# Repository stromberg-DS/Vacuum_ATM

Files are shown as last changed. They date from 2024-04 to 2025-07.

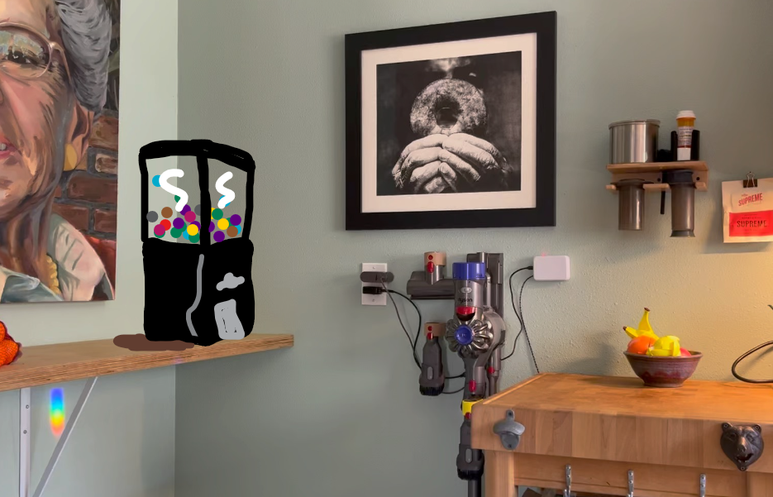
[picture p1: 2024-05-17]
Images/OriginalLocation.png

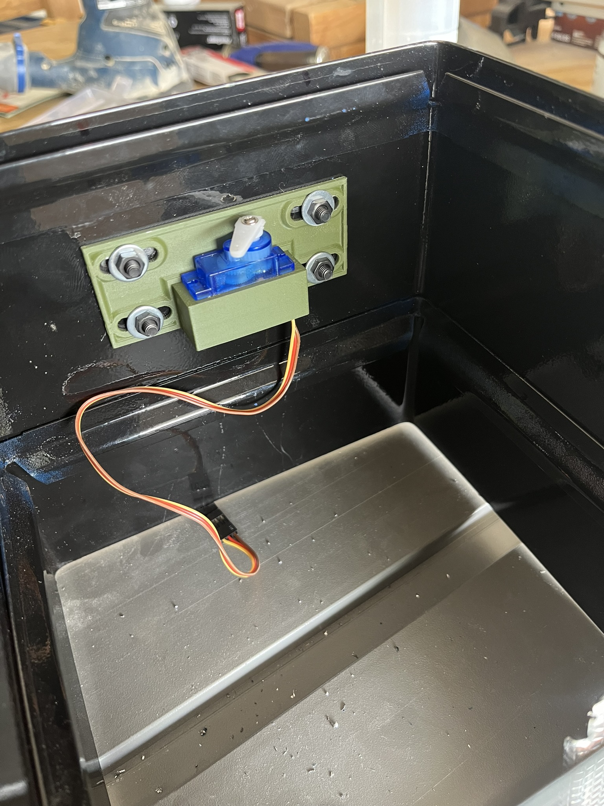
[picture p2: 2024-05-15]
Images/ServoMount.JPEG

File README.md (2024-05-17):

# Vacuum_ATM
Automatically reward the first person who vacuums the floor.

This is a project that tracks the dust levels in your house and tells you when to vacuum. A Photon 2 microcontroller detects when the vacuum is removed/replaced. Meanwhile a separate Photon 2 mounted inside a toy vending machine tracks if you have vacuumed for long enough to get a reward. If you have vacuumed long enough, you can turn the crank and get a plastic capsule filled with whatever (money, candy, etc).

## Directory

**Vacuum_ATM** - This folder contains the code for the dispensing side of the system.

**Vacuum_Status** - This folder contains the code for the photon that senses the presence of the vacuum.

**3D_Models** - Models to print out to get everything to work.

**Cut_Files** - Files to cut on a CNC router or laser cutter.

**Wiring Diagram** - Images of the wiring of both the Vacuum ATM and the Vacuum Status Photons.

**Testing** - Where I did all of my initial R&D. Actually I'm kind of embarassed that you would even want to look in here. Go back up to 3D_models. This is not a good look for you.

More information can be found at [my Hackster.io writeup](https://www.hackster.io/blotlat/vacuum-atm-a74ef9)

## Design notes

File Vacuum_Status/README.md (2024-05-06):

# Vacuum_Status

This firmware project was created using [Particle Developer Tools](https://www.particle.io/developer-tools/) and is compatible with all [Particle Devices](https://www.particle.io/devices/).

Feel free to replace this README.md file with your own content, or keep it for reference.

## Table of Contents
- [Introduction](#introduction)
- [Prerequisites To Use This Template](#prerequisites-to-use-this-repository)
- [Getting Started](#getting-started)
- [Particle Firmware At A Glance](#particle-firmware-at-a-glance)
  - [Logging](#logging)
  - [Setup and Loop](#setup-and-loop)
  - [Delays and Timing](#delays-and-timing)
  - [Testing and Debugging](#testing-and-debugging)
  - [GitHub Actions (CI/CD)](#github-actions-cicd)
  - [OTA](#ota)
- [Support and Feedback](#support-and-feedback)
- [Version](#version)

## Introduction

For an in-depth understanding of this project template, please refer to our [documentation](https://docs.particle.io/firmware/best-practices/firmware-template/).

## Prerequisites To Use This Repository

To use this software/firmware on a device, you'll need:

- A [Particle Device](https://www.particle.io/devices/).
- Windows/Mac/Linux for building the software and flashing it to a device.
- [Particle Development Tools](https://docs.particle.io/getting-started/developer-tools/developer-tools/) installed and set up on your computer.
- Optionally, a nice cup of tea (and perhaps a biscuit).

## Getting Started

1. While not essential, we recommend running the [device setup process](https://setup.particle.io/) on your Particle device first. This ensures your device's firmware is up-to-date and you have a solid baseline to start from.

2. If you haven't already, open this project in Visual Studio Code (File -> Open Folder). Then [compile and flash](https://docs.particle.io/getting-started/developer-tools/workbench/#cloud-build-and-flash) your device. Ensure your device's USB port is connected to your computer.

3. Verify the device's operation by monitoring its logging output:
    - In Visual Studio Code with the Particle Plugin, open the [command palette](https://docs.particle.io/getting-started/developer-tools/workbench/#particle-commands) and choose "Particle: Serial Monitor".
    - Or, using the Particle CLI, execute:
    ```
    particle serial monitor --follow
    ```

4. Uncomment the code at the bottom of the cpp file in your src directory to publish to the Particle Cloud! Login to console.particle.io to view your devices events in real time.

5. Customize this project! For firmware details, see [Particle firmware](https://docs.particle.io/reference/device-os/api/introduction/getting-started/). For information on the project's directory structure, visit [this link](https://docs.particle.io/firmware/best-practices/firmware-template/#project-overview).

## Particle Firmware At A Glance

### Logging

The firmware includes a [logging library](https://docs.particle.io/reference/device-os/api/logging/logger-class/). You can display messages at different levels and filter them:

```
Log.trace("This is trace message");
Log.info("This is info message");
Log.warn("This is warn message");
Log.error("This is error message");
```

### Setup and Loop

Particle projects originate from the Wiring/Processing framework, which is based on C++. Typically, one-time setup functions are placed in `setup()`, and the main application runs from the `loop()` function.

For advanced scenarios, explore our [threading support](https://docs.particle.io/firmware/software-design/threading-explainer/).

### Delays and Timing

By default, the setup() and loop() functions are blocking whilst they run, meaning that if you put in a delay, your entire application will wait for that delay to finish before anything else can run. 

For techniques that allow you to run multiple tasks in parallel without creating threads, checkout the code example [here](https://docs.particle.io/firmware/best-practices/firmware-template/).

(Note: Although using `delay()` isn't recommended for best practices, it's acceptable for testing.)

### Testing and Debugging

For firmware testing and debugging guidance, check [this documentation](https://docs.particle.io/troubleshooting/guides/build-tools-troubleshooting/debugging-firmware-builds/).

### GitHub Actions (CI/CD)

This project provides a YAML file for GitHub, automating firmware compilation whenever changes are pushed. More details on [Particle GitHub Actions](https://docs.particle.io/firmware/best-practices/github-actions/) are available.

### OTA

To learn how to utilize Particle's OTA service for device updates, consult [this documentation](https://docs.particle.io/getting-started/cloud/ota-updates/).

Test OTA with the 'Particle: Cloud Flash' command in Visual Studio Code or the CLI command 'particle flash'!

This firmware supports binary assets in OTA packages, allowing the inclusion of audio, images, configurations, and external microcontroller firmware. More details are [here](https://docs.particle.io/reference/device-os/api/asset-ota/asset-ota/).

## Support and Feedback

For support or feedback on this template or any Particle products, please join our [community](https://community.particle.io)!

## Version

Template version 1.0.2

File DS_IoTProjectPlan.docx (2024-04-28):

Project Name: Vacuum ATM
Student Name: Daniel Stromberg | Capstone Date:5/17/24

Project Motivation and Overview:

With 2 dogs and a cat, my house needs frequent vacuuming. Vacuuming always falls off the radar. The Vacuum ATM will incentivize anyone in the house to vacuum by dispensing a reward (cash or otherwise) after they vacuum. The Vacuum ATM will lock out any more rewards for several days, showing an alert when it is ready to give out another reward.

Cash will be dispensed either with rollers and a stepper motor, or through a modified capsule toy vending machine.

Minimum Features:

- Track the accumulation of dust over time.
- Track the amount of time that has passed since the last time the vacuum was used.
- Track whether the vacuum is charging or in use.
- Alert the household when the vacuum is ready to be used (when a reward will be dispensed for vacuuming). A simple LED would be a basic option.
- Reward the person who vacuumed (Basic option would be credits or leaderboard shown on a dashboard)

Desired Features:

- Show vacuum use on a dashboard (dust levels, how long until vacuum is ready, etc.).
- Dispense dollar bills (or other incentive) when user has vacuumed long enough.
- Send a text/email to let house members know the vacuum is ready to reward someone for vacuuming.

Stretch Goal Features:

- Get weather data and increase vacuuming frequency if wind is high.
- Detect who vacuumed (separate buttons).
- Use fingerprint sensor to ID who has vacuumed.

Anticipated Components:

- Reed Switch or Hall effect sensor
- ~~Stepper Motor & controller board (large motor if using toy dispenser)~~ – updated 4/28, opting for other option.
- Neopixels
- Fingerprint sensor

Concerns and Considerations (Project Risks and Potential Mitigations)

- How to detect if someone actually vacuums vs taking it off the wall, doing nothing, and replacing it?
- How to dispense rewards?

Other Information:

Project Implementation Timeline:
Tasks | 12-APR | 19-APR | 26-APR | 3-May | 10-May | 17-May
Project Plan | X
Plan Dispenser, order parts | | X
Make overall design | | | X
Test Vacuum logic w/basic parts | | | X
Design display | | | X
Build/assemble dispenser | | | | X
Final Assembly | | | | | X
Finish Hackster.io | | | | | X
Edit Video | | | | | | X
Finish Presentation & Video | | | | | | X
Capstone Presentation | | | | | | X

Internet of Things and Rapid Prototyping Bootcamp – Capstone Project Proposal

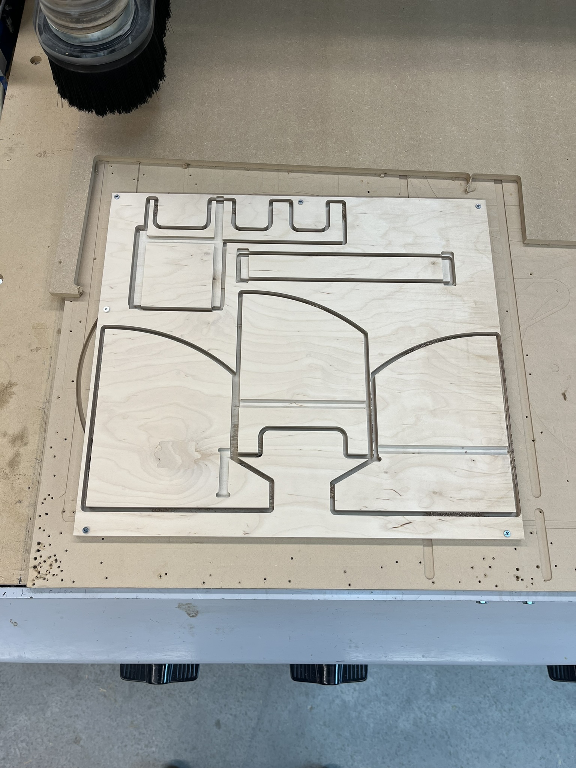
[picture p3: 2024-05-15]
Images/Panels.JPEG

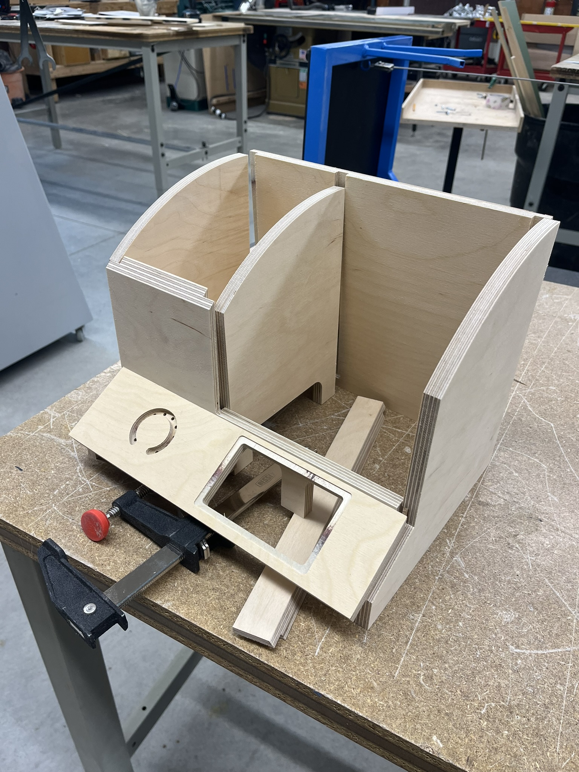
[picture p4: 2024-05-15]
Images/DryFit.JPEG

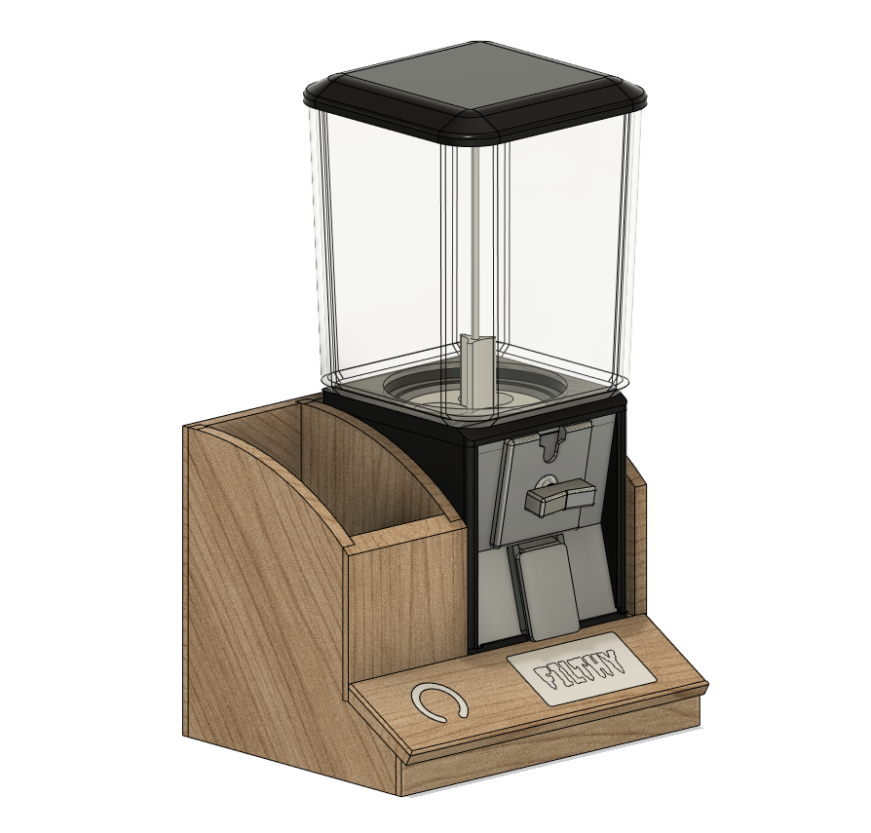
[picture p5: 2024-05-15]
Images/VacATM.png

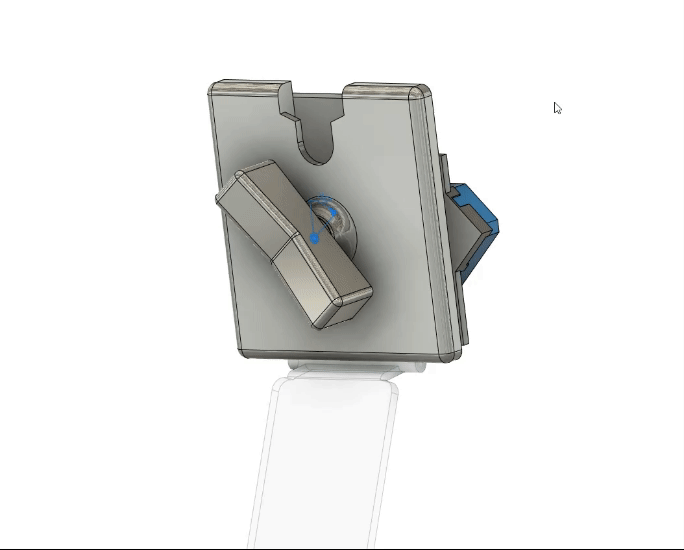
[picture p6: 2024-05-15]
Images/KnobTurning.gif

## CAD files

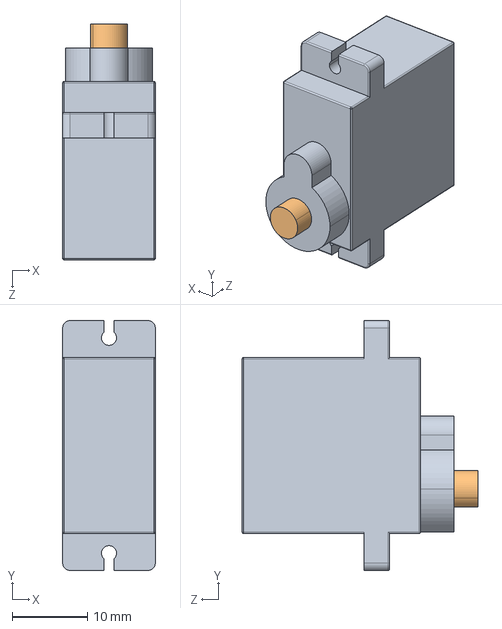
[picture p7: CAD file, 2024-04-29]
3D_Models/serwo 9g.STEP
12.3 x 33.2 x 31.3 mm
korpus
wał

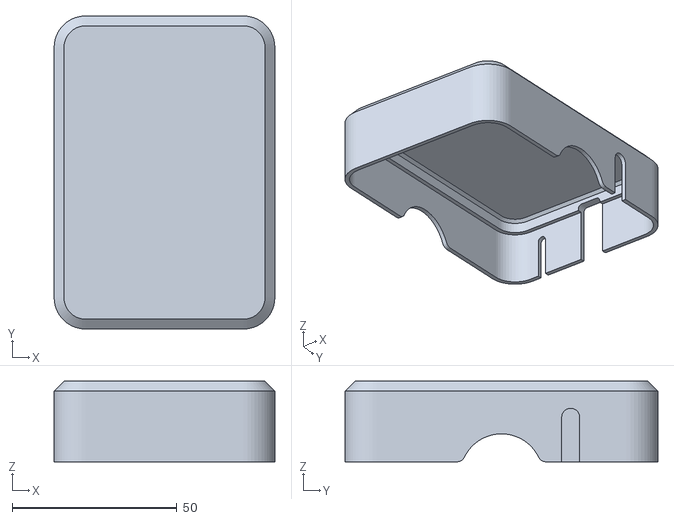
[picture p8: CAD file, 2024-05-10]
3D_Models/VacStatus_Case/CaseTop.stl
67.0 x 95.0 x 24.5

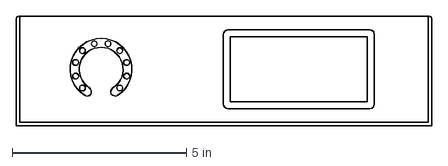
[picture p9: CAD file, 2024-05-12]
Cut_Files/Faceplate.dxf
11.9 x 3.15 in

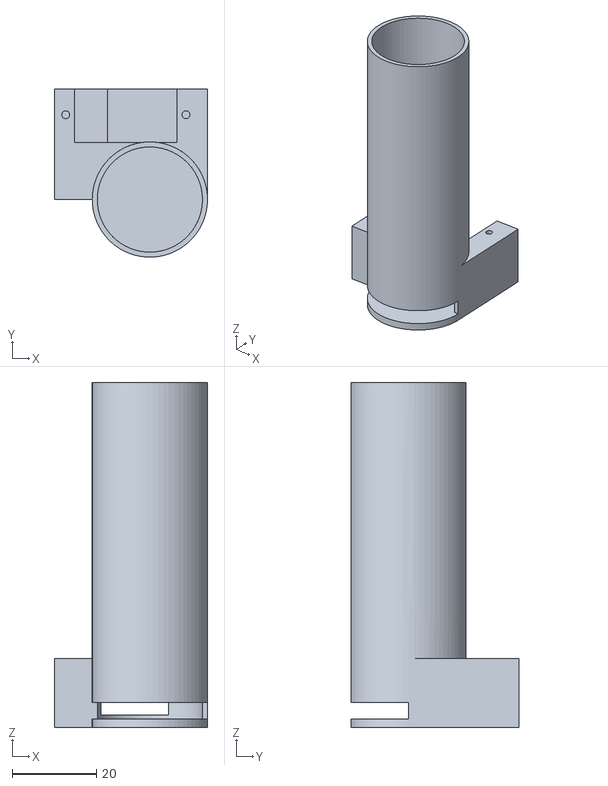
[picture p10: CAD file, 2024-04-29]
DispenseTube.stl
36.4 x 40.0 x 82.0

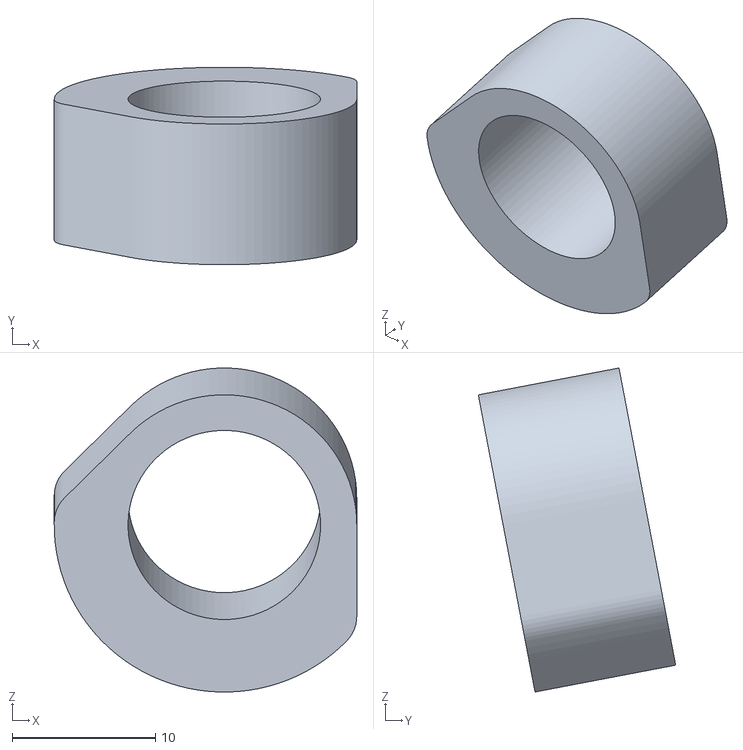
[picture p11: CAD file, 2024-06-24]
3D_Models/ATM_models/SwitchCam.stl
21.1 x 13.8 x 22.6

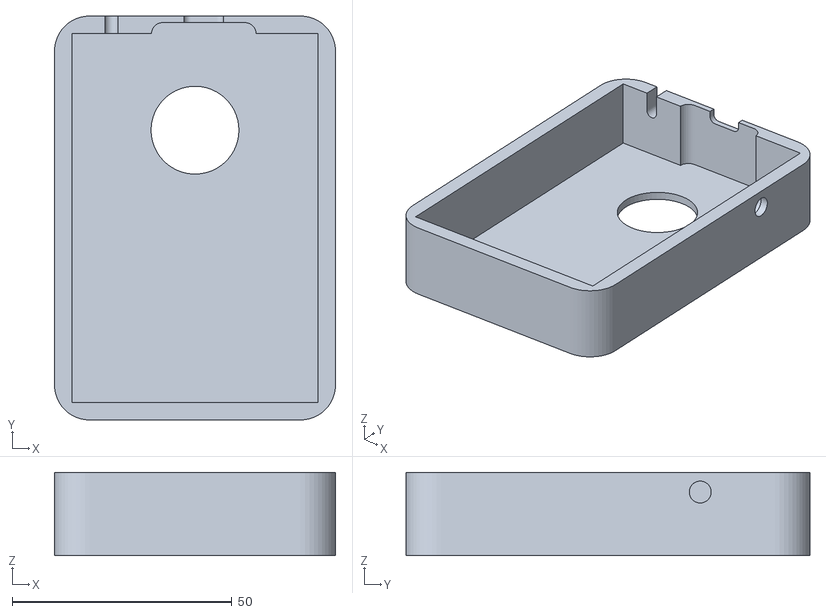
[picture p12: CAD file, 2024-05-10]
3D_Models/VacStatus_Case/CaseBottom.stl
64.0 x 92.0 x 19.0

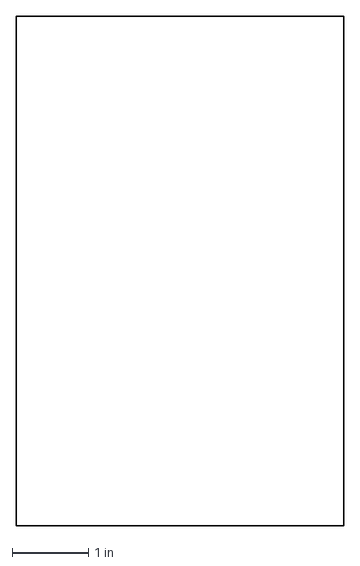
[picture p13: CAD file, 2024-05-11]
Cut_Files/Shelf.dxf
4.29 x 6.68 in

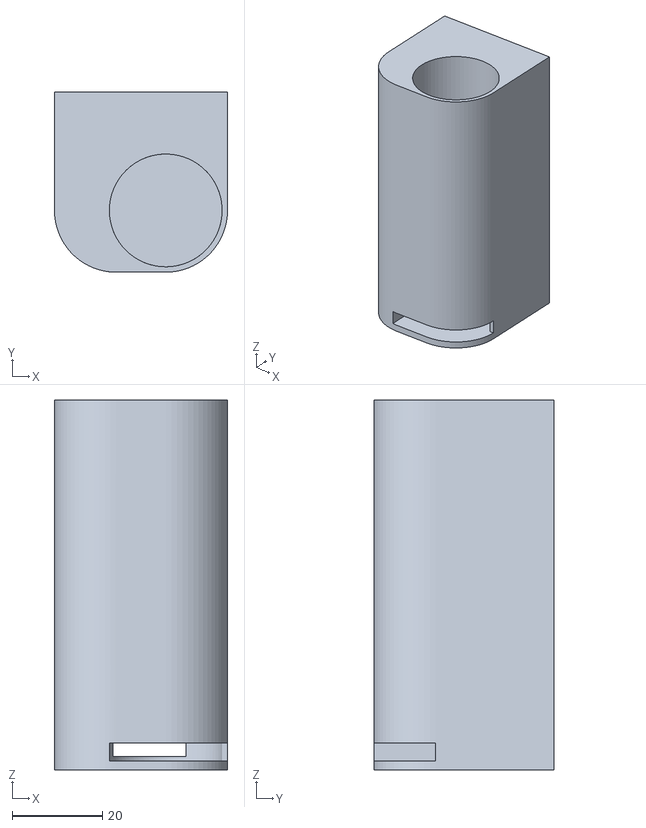
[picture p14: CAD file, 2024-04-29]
DispenseTubeV3.stl
38.4 x 40.0 x 82.0

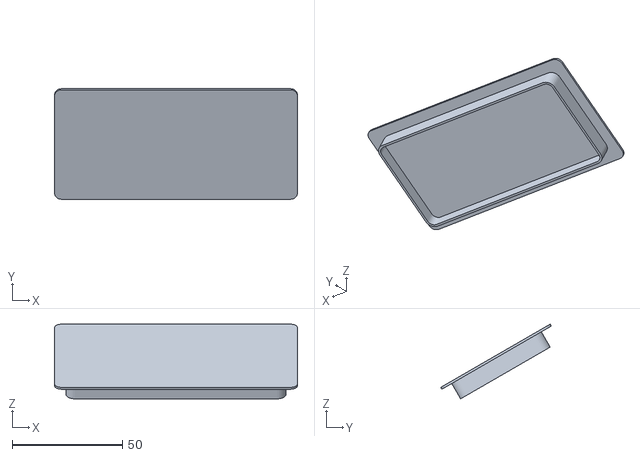
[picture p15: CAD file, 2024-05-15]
3D_Models/ATM_models/Display.stl
110.0 x 50.1 x 33.8

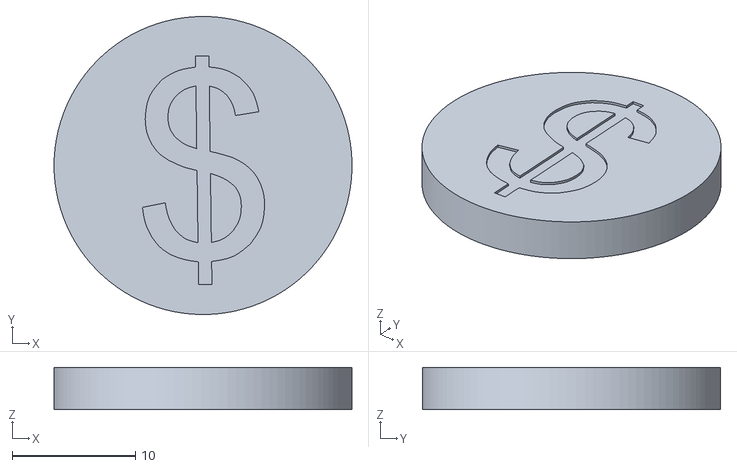
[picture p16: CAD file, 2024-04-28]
Coin.stl
24.2 x 24.2 x 3.43

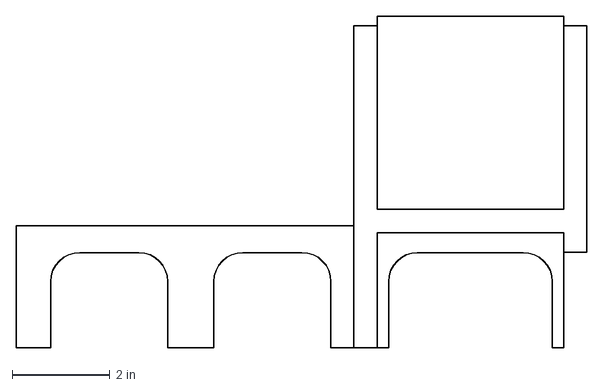
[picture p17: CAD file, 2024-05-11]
Cut_Files/Front.dxf
11.7 x 6.79 in

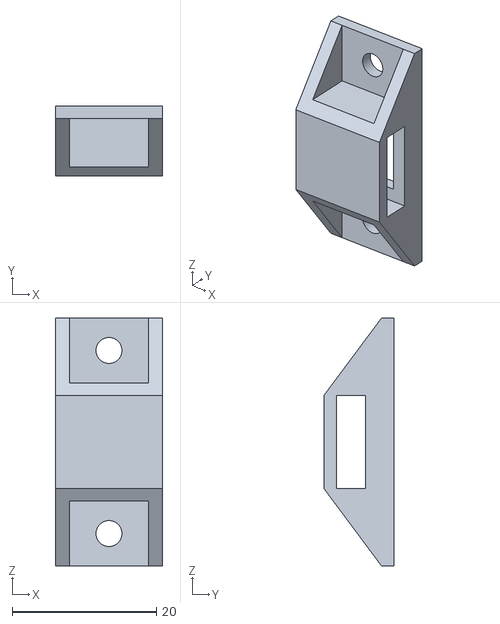
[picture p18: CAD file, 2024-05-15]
3D_Models/ATM_models/ButtonMount.stl
14.9 x 9.75 x 34.4

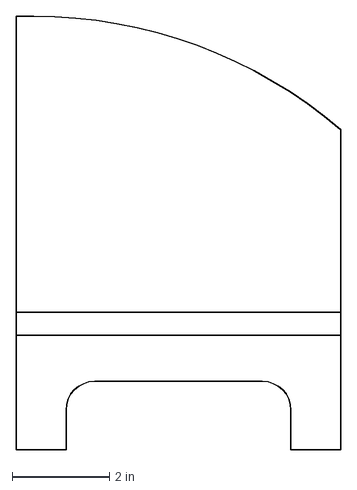
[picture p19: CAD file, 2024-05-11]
Cut_Files/Middle.dxf
6.68 x 8.93 in

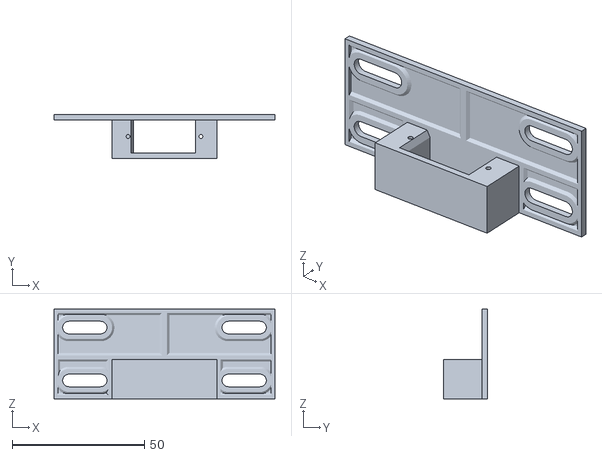
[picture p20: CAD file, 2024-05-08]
3D_Models/ATM_models/Servomount.stl
83.5 x 16.5 x 34.0

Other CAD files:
Cut_Files/Right.dxf
3D_Models/ATM_models/smSwitchMount.stl
Cut_Files/Back.dxf
3D_Models/ATM_models/HoleCover.stl
3D_Models/ATM_models/ShaftCollar.stl
3D_Models/ATM_models/SwitchCam_wSetScrew.stl
Cut_Files/FaceSupport.dxf
Cut_Files/Left.dxf

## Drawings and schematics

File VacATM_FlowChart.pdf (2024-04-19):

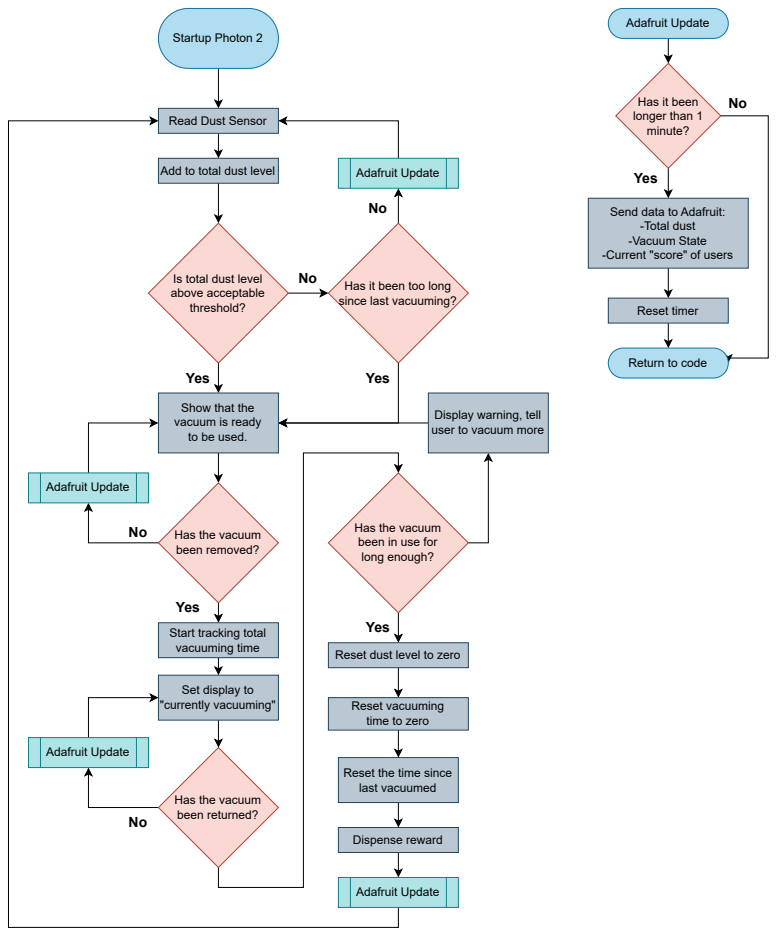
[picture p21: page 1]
Yes; Dispense reward; Startup Photon 2; Adafruit Update; Reset timer

Has it been
longer than 1
minute?

Read Dust Sensor

Add to total dust level

Send data to Adafruit:
-Total dust
-Vacuum State
-Current "score" of users

Is total dust level
above acceptable
threshold?

Has it been too long
since last vacuuming?

Return to code

Show that the
vacuum is ready
to be used.

Display warning, tell
user to vacuum more

Has the vacuum
been in use for
long enough?

been removed?

Start tracking total
vacuuming time

Reset dust level to zero

Set display to
"currently vacuuming"

Reset vacuuming
time to zero

Reset the time since
last vacuumed

been returned?

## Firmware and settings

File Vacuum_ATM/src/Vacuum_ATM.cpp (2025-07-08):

/* 
 * Get Dust & Vacuum General Logic
 * Get dust values from plant. Test vacuum logic and timing.
 * 
 * Author: Daniel Stromberg
 * Date: 4/20/24
*/

#include "Particle.h"
#include <Adafruit_MQTT.h>
#include "Adafruit_MQTT/Adafruit_MQTT_SPARK.h"
#include "Adafruit_MQTT/Adafruit_MQTT.h"
#include "credentials.h"
#include <neopixel.h>
#include "Button_DS.h"
#include "Timer_DS.h"


SYSTEM_MODE(AUTOMATIC);
SYSTEM_THREAD(ENABLED);

const int PIXEL_COUNT = 33;
const int RING_PIXEL_MIN = 1;   //first pixel to light on ring
const int RING_PIXEL_MAX = 15;
const int STRIP_PIXEL_MIN = 16; //first pixel on strip
const int STRIP_PIXEL_MAX = 33; //last pixel on strip
const int PUBLISH_TIME = 30000;
const int RED = 0xFF0000;     //not ready to vacuum
const int REDDISH_RING = 0x991100;
const int REDDISH_STRIP = 0xFF2200;
const int YELLOWISH_RING = 0x553300;
const int GREENISH_RING = 0X15fe09;
const int BLUE = 0x0000FF;    //successfully vacuumed!
const int GREEN = 0x00FF00;   //ready to vacuum
const int YELLOW = 0xFFFF00;  //currently vacuuming
const int MAGENTA = 0xFF00FF; //need more vacuuming
const int WHITE = 0xFFFFFF;        //Take a reward!
const int BASELINE_BRIGHTNESS = 50;
const int SERVO_PIN = A5;
const int SERVO_CLOSED = 140; //door is closed
const int SERVO_OPEN = 10;
const int CAM_PIN = D3;     //changed from D18 - my PCB is weird and D18 is connected to A5. BAD!
const int VAC_PIN = A2;

//Vacuum States
int vacuumState;
int lastVacuumState;
const int CHARGING_NOT_DIRTY = 0; //red
const int CHARGING_YES_DIRTY = 1; //green
const int NOW_VACUUM_NO_REWARD = 2; //yellow
const int NOW_VACUUM_REWARD_READY =3; //
const int STOPPED_EARLY = 4;
const int FINISHED_TAKE_REWARD = 5;
const String VAC_STATE_STRING[6] = {"Charging, not dirty.", "Charging, dirty", "Vacuuming, reward not ready",
                                    "Vacuuming, reward ready", "Stopped early", "Finished, take reward"};
int vacStartTime;
int elapsedVacTime=0;   //total time spent vacuuming
int prevVacTime = 0;    //previous total time vacuuming
int lastVacStateTime;   //last time the vacuum state changed
bool isReadyToDispense = false; //After vacuum is returned & has been used enough set true
bool isVacCharging;
bool lastVacChargeState;
unsigned int timeSinceVacuumed;
bool isVacReturned = 0;
bool isVacRemoved = 0;


const int VACUUMING_TIME = 600000;   //900,000 is 15 min, 600,000 = 10 min
const int MAX_DUST = 3000000;       //3,500,000 - roughly 1 week @500 particles/15 min 
const int MAX_TIME_SINCE_VAC = 1209600;            //time in seconds - 1,209,600sec = 14 days

//EEPROM Setup
int len = EEPROM.length();
int totalDustAddress = 0x0001; //4 bytes from 0x0001 to 0x0004
int timeAddress = 0x0010;   //

bool isLEDOn = false;
unsigned int totalDust = 0; //4 bytes - 
float totalDustK = 0;
int lastRXTime = 0;
int ringLEDDustLevel = 0;
int ringVacTimeLevel = 0;

//Time
unsigned int previousUnixTime;
unsigned int currentUnixTime;
unsigned int incomingStateChangeTime;
time32_t now();

//Functions
void MQTT_connect();
bool MQTT_ping();
void getNewDustData();
void adaPublish();
void dustToBytes(int dustIn, byte *dustHOut, byte *dustMOut, byte *dustLOut);
void newDataLEDFlash();
void fillLEDs(int ledColor, int startLED=0, int lastLED=PIXEL_COUNT);
void breatheLEDs(int ledColor, int startLED=0, int lastLED=PIXEL_COUNT);
void checkLEDs(int ledColor, int startLED, int lastLED);
void moveServo(int position);
void periodicPrint();

TCPClient TheClient;
Adafruit_MQTT_SPARK mqtt(&TheClient, AIO_SERVER, AIO_SERVERPORT, AIO_USERNAME, AIO_KEY);
Adafruit_MQTT_Subscribe dustSub = Adafruit_MQTT_Subscribe(&mqtt, AIO_USERNAME "/feeds/plantinfo.dustsensor");
Adafruit_MQTT_Subscribe vacInfoSub = Adafruit_MQTT_Subscribe(&mqtt, AIO_USERNAME "/feeds/vacuumstatus");
Adafruit_MQTT_Publish dustPub = Adafruit_MQTT_Publish(&mqtt, AIO_USERNAME "/feeds/totaldust");

// Timer publishTimer(PUBLISH_TIME, adaPublish);

Adafruit_NeoPixel pixel(PIXEL_COUNT, SPI1, WS2812);
Servo myServo;
Button vacButton(VAC_PIN);
Button camButton(CAM_PIN);
IoTTimer flashTimer;
IoTTimer servoTimer;

void setup() {
    Serial.begin(9600);
    waitFor(Serial.isConnected, 10000);

    Watchdog.init(WatchdogConfiguration().timeout(600s));     //Set watchdog timer to 5 min
    Watchdog.start();                                         //Start watchdog timer

    myServo.attach(SERVO_PIN);
    moveServo(SERVO_CLOSED);
    pixel.begin();
    pixel.setBrightness(BASELINE_BRIGHTNESS);

    checkLEDs(0x000099, RING_PIXEL_MAX, RING_PIXEL_MIN);
    checkLEDs(0, RING_PIXEL_MAX, RING_PIXEL_MIN);

    checkLEDs(0xFF0000, STRIP_PIXEL_MAX, STRIP_PIXEL_MIN);
    checkLEDs(0, STRIP_PIXEL_MAX, STRIP_PIXEL_MIN);
    pixel.clear();
    pixel.show();


    Serial.printf("Connecting to Particle cloud...");
    while(!Particle.connected()){
        //wait to connect to particle cloud
    }

    previousUnixTime = EEPROM.get(timeAddress, previousUnixTime);
    Serial.printf("PreviousTime: %u\n\n", previousUnixTime);


    totalDust = EEPROM.get(totalDustAddress, totalDust);
    ringLEDDustLevel = map(totalDust, 0, MAX_DUST, RING_PIXEL_MAX, RING_PIXEL_MIN);
    ringLEDDustLevel = constrain(ringLEDDustLevel, RING_PIXEL_MIN, RING_PIXEL_MAX);
    fillLEDs(0x330000, RING_PIXEL_MIN, ringLEDDustLevel);
    pixel.show();
    // publishTimer.start();

    mqtt.subscribe(&dustSub);
    mqtt.subscribe(&vacInfoSub);

    pinMode(7, OUTPUT);
    digitalWrite(7, LOW);

}

void loop() {
  Watchdog.refresh();
    MQTT_connect();
    MQTT_ping();

    currentUnixTime = Time.now();
    timeSinceVacuumed = currentUnixTime - previousUnixTime;

    if(vacuumState != lastVacuumState){
        Serial.printf("New Vacuum State:\n  %s\n\n", VAC_STATE_STRING[vacuumState].c_str());
        lastVacStateTime = millis();    //track when state changes
        lastVacuumState = vacuumState;
    }

    // periodicPrint();
    getNewDustData();
    newDataLEDFlash();


  ////Treat button like real vacuum
  ////  pressed = vacuum on charger
  ////  released = taking off charger
  ////  not pressed = vacuuming
  ////  clicked = putting back on charger
  //
  //If the house is dirty or it has been too long...
  if((totalDust > MAX_DUST) || (timeSinceVacuumed>MAX_TIME_SINCE_VAC)){
    ringVacTimeLevel = map(elapsedVacTime, 0, VACUUMING_TIME, RING_PIXEL_MAX, RING_PIXEL_MIN);
    ringVacTimeLevel = constrain(ringVacTimeLevel, RING_PIXEL_MIN, RING_PIXEL_MAX);
    fillLEDs(REDDISH_RING, RING_PIXEL_MIN, RING_PIXEL_MAX);
    fillLEDs(GREENISH_RING, ringVacTimeLevel, RING_PIXEL_MAX);
    fillLEDs(REDDISH_STRIP, STRIP_PIXEL_MIN, STRIP_PIXEL_MAX);

    // fillLEDs(REDDISH_RING, RING_PIXEL_MIN, RING_PIXEL_MAX);
    // fillLEDs(REDDISH_STRIP, STRIP_PIXEL_MIN, STRIP_PIXEL_MAX);
    vacuumState = CHARGING_YES_DIRTY;


    if(isVacRemoved){      //When vacuum removed
      vacStartTime = millis();        //set the start vacuum timer 
      isVacRemoved = false;
    }
    //if you are vacuuming
    if(!isVacCharging){
      elapsedVacTime = prevVacTime+ (millis() - vacStartTime);
      // ringVacTimeLevel = map(elapsedVacTime, 0, VACUUMING_TIME, RING_PIXEL_MAX, RING_PIXEL_MIN);
      // ringVacTimeLevel = constrain(ringVacTimeLevel, RING_PIXEL_MIN, RING_PIXEL_MAX);
      if(elapsedVacTime > VACUUMING_TIME){  //check if you have vacuumed long enough
        fillLEDs(GREENISH_RING, RING_PIXEL_MIN, RING_PIXEL_MAX);
        fillLEDs(0, STRIP_PIXEL_MIN, STRIP_PIXEL_MAX);
        vacuumState = NOW_VACUUM_REWARD_READY;
      } else{
        // fillLEDs(REDDISH_RING, RING_PIXEL_MIN, RING_PIXEL_MAX);
        // fillLEDs(0x553300, ringVacTimeLevel, RING_PIXEL_MAX);
        // fillLEDs(REDDISH_STRIP, STRIP_PIXEL_MIN, STRIP_PIXEL_MAX);
        vacuumState = NOW_VACUUM_NO_REWARD;
      }
    }
    //If the vacuum is returned
    if(isVacReturned){         
      isVacReturned = false;
      if(elapsedVacTime > VACUUMING_TIME){  //check if you have vacuumed enough
        totalDust =0;
        totalDustK = 0;
        timeSinceVacuumed = 0;
        elapsedVacTime =0;
        prevVacTime = 0;
        previousUnixTime = currentUnixTime;
        EEPROM.put(timeAddress, currentUnixTime);   //log last vacuum time in EEPROM
        vacuumState = FINISHED_TAKE_REWARD;
        isReadyToDispense = true;
      }else{
        isReadyToDispense = false;
        prevVacTime = elapsedVacTime;
        vacuumState = STOPPED_EARLY;
        flashTimer.startTimer(2000);
      }
    }
  }else{    //If the house is not dirty enough

    pixel.clear();
    fillLEDs(0x553300, RING_PIXEL_MIN, RING_PIXEL_MAX);
    fillLEDs(REDDISH_RING, ringLEDDustLevel, RING_PIXEL_MAX);
    vacuumState = CHARGING_NOT_DIRTY;
  }

if(isReadyToDispense){
  fillLEDs(0x443322, RING_PIXEL_MIN, RING_PIXEL_MAX);
  fillLEDs(0, STRIP_PIXEL_MIN, STRIP_PIXEL_MAX);
  if(camButton.isClicked()){
    moveServo(SERVO_OPEN);
    Serial.printf("Door opening - cam clicked\n");
  } else if (camButton.isReleased()){
    isReadyToDispense = false;
    moveServo(SERVO_CLOSED);
    ringLEDDustLevel = RING_PIXEL_MAX;
    pixel.clear();
  }
}

    pixel.show();
}

void moveServo(int position){
    position = constrain(position, 0, 180);
    myServo.write(position);
    delay(500);
    // Serial.printf("!!!!!!!MOVING SERVO: %i!!!!!!!\n!!!!!!!!!!!!!!!!!!!!!!!!!!!!\n\n", position);
}

void periodicPrint(){
  static int lastPrintTime;

  if(millis()-lastPrintTime > 1000){
        // Serial.printf("Dust: %i\nTime: %i\nTotal Vac time: %i\n", totalDust, timeSinceVacuumed,elapsedVacTime);
        Serial.printf("CamButton: %i\n\n", camButton.isPressed());
        lastPrintTime = millis();
    }
}

void fillLEDs(int ledColor, int startLED, int lastLED){
  if(startLED < lastLED){
    for(int i=startLED; i<lastLED; i++){
        pixel.setPixelColor(i, ledColor);
    }
  }
}

void breatheLEDs(int ledColor, int startLED, int lastLED){

}

void checkLEDs(int ledColor, int startLED, int lastLED){
  for(int i=startLED; i>lastLED; i--){
      // pixel.clear();
      pixel.setPixelColor(i, ledColor);
      pixel.show();
      delay(50);
    }
}

//Wait for new dust data and save it to the EEPROM
void getNewDustData(){
    int incomingDust;
    String incomingVacInfo;

    Adafruit_MQTT_Subscribe *subscription;
    while((subscription = mqtt.readSubscription(100))){
        if(subscription == &dustSub){
            incomingDust = strtol((char *)dustSub.lastread,NULL,10);
            Serial.printf("Int incoming dust: %i\n", incomingDust);
            totalDust = totalDust + incomingDust;
            EEPROM.put(totalDustAddress, totalDust);

            ringLEDDustLevel = map(totalDust, 0, MAX_DUST, RING_PIXEL_MAX, RING_PIXEL_MIN);
            ringLEDDustLevel = constrain(ringLEDDustLevel, RING_PIXEL_MIN, RING_PIXEL_MAX);
            Serial.printf("Ring LED #%i\n\n", ringLEDDustLevel);
            totalDustK = totalDust / 1000.0;    //divide by 1,000 for nicer visualization
            lastRXTime = millis();
            Serial.printf("%0.2fk Total Dust Particles\n\n", totalDustK);
            adaPublish();
        } else if (subscription == &vacInfoSub){
            lastRXTime = millis();
            incomingStateChangeTime = Time.now();
            incomingVacInfo = (char *)vacInfoSub.lastread;
            isVacCharging = atoi(incomingVacInfo);
            
            //VacStatus Photon only sends chargin/not charging on state change
            //  so we can assume the below are the rising/falling edge of state change
            isVacReturned = isVacCharging;
            isVacRemoved = !isVacCharging;

            Serial.printf("### vac info incoming ###\n");
            Serial.printf("isVacCharging: %i\n", isVacCharging);
            Serial.printf("Last Vac state change time: %u\n\n", incomingStateChangeTime);
        }
    }

    

}


//Flash onboard LED when new data comes in
void newDataLEDFlash(){
    if(millis() - lastRXTime <500){
        digitalWrite(7, HIGH);  
    } else{
        digitalWrite(7, LOW);
    }
}

//Publish to Adafruit.io - dust is divided by 1,000 for legibility
void adaPublish(){
  if(mqtt.Update()){
    dustPub.publish(totalDustK);
  }
}

// Function to connect and reconnect as necessary to the MQTT server.
// Should be called in the loop function and it will take care of connecting.
void MQTT_connect(){
    int8_t ret;

    // Return if already connected.
    if (mqtt.connected()){
        return;
    }

    Serial.print("Connecting to MQTT... ");

    while((ret = mqtt.connect()) != 0){
        Serial.printf("Error Code %s\n", mqtt.connectErrorString(ret));
        Serial.printf("Retrying MQTT connection in 5 seconds...\n");
        mqtt.disconnect();
        delay(5000);
    }
    Serial.printf("MQTT Connected!\n");
}

//Keeps the connection open to Adafruit
bool MQTT_ping() {
    static unsigned int last;
    bool pingStatus;

    if ((millis()-last)>120000) {
        Serial.printf("Pinging MQTT \n");
        pingStatus = mqtt.ping();
        if(!pingStatus) {
        Serial.printf("Disconnecting \n");
        mqtt.disconnect();
        }
        last = millis();
    }
    return pingStatus;
}

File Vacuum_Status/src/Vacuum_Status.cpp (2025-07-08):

/* 
 * Vacuum ATM - Vacuum Status Detector
 * Author: Daniel Stromberg
 * Date: 5/5/24
*/

#include "Particle.h"
#include "credentials.h"
#include "Button_DS.h"
#include "neopixel.h"
#include <Adafruit_MQTT.h>
#include "Adafruit_MQTT/Adafruit_MQTT_SPARK.h"
#include "Adafruit_MQTT/Adafruit_MQTT.h"
#include <math.h>


SYSTEM_MODE(AUTOMATIC);
SYSTEM_THREAD(ENABLED);

const int RED_LED_PIN = D1;

bool isVacCharging;
bool lastVacState;
unsigned int stateChangeUnixTime;
String pubInfoString;
float t;
float ledBrightness;

//Functions
void MQTT_connect();
void adaPublish();
bool MQTT_ping();

TCPClient TheClient;
Adafruit_MQTT_SPARK mqtt(&TheClient, AIO_SERVER, AIO_SERVERPORT, AIO_USERNAME, AIO_KEY);
Adafruit_MQTT_Publish vacStatus = Adafruit_MQTT_Publish(&mqtt, AIO_USERNAME "/feeds/vacuumstatus");


Button vacButton(A2);

void noUglyLEDs();
void lightRedLED();

void setup() {
    Serial.begin(9600);
    waitFor(Serial.isConnected, 10000);

    pinMode(RED_LED_PIN, OUTPUT);
    pinMode(D7, OUTPUT);
    digitalWrite(D7, LOW);

    Watchdog.init(WatchdogConfiguration().timeout(600s));   //Set watchdog timer to 5 min
    Watchdog.start();
}

void loop() {
    Watchdog.refresh();     //Watchdog timer checks in every loop
    MQTT_connect();
    MQTT_ping();
    isVacCharging = vacButton.isPressed();

    lightRedLED();
    
    if(isVacCharging != lastVacState){
        Serial.printf("Status changed! Send to adafruit!\nCharging: %i\nCurrent Time: %u\n\n", isVacCharging, stateChangeUnixTime);
        lastVacState = isVacCharging;

        // I was planning to send vacuum status and time together, but changed my mind
        // 
        // stateChangeUnixTime = Time.now();
        // pubInfoString = String(isVacCharging)+String(stateChangeUnixTime);      //Add current vacuum state onto beginning of string
        // Serial.printf("%s\n\n", pubInfoString.c_str());

        adaPublish();       //send state to adafruit 
    }

    noUglyLEDs();  
}

//Pulse red LED when vacuum is charging
void lightRedLED(){
    if(isVacCharging){
        t = fmod((millis()/1000.0 + 0.5), 4.0) ;         //Keeps T between 0.0-4.0 to make calculation easier.
        ledBrightness = 23 * sin(2*M_PI*t/4.0)+28;
        analogWrite(RED_LED_PIN, ledBrightness);
    }else{
        digitalWrite(RED_LED_PIN, 0);
    }
}

//turn off other onboard LEDs
void noUglyLEDs(){
    if((millis()>20000)&&(Particle.connected)){
        RGB.control(true);
        RGB.brightness(0);
    } else{
        RGB.control(false);
    }
}

//Publish to Adafruit.io
void adaPublish(){
  if(mqtt.Update()){
    vacStatus.publish(isVacCharging);
  }
}

// Function to connect and reconnect as necessary to the MQTT server.
// Should be called in the loop function and it will take care of connecting.
void MQTT_connect(){
    int8_t ret;

    // Return if already connected.
    if (mqtt.connected()){
        return;
    }


    Serial.print("Connecting to MQTT... ");

    while((ret = mqtt.connect()) != 0){
        Serial.printf("Error Code %s\n", mqtt.connectErrorString(ret));
        Serial.printf("Retrying MQTT connection in 5 seconds...\n");
        mqtt.disconnect();
        delay(5000);
    }
    Serial.printf("MQTT Connected!\n");
}

//Keeps the connection open to Adafruit
bool MQTT_ping() {
    static unsigned int last;
    bool pingStatus;

    if ((millis()-last)>120000) {
        Serial.printf("Pinging MQTT \n");
        pingStatus = mqtt.ping();
        if(!pingStatus) {
        Serial.printf("Disconnecting \n");
        mqtt.disconnect();
        }
        last = millis();
    }
    return pingStatus;
}

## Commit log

2024-04-19 Added flowchart
2024-04-19 Threaded dust sensor working. Updating to Adafruit
2024-04-19 Testing fingerprint sensor, no luck yet
2024-04-21 Testing fingerprint code
2024-04-22 Total dust level remaining through resets
    [GetDust_VacLogic.cpp]
2024-04-22 Added button class
2024-04-22 Added a vacuum-simulator button
2024-04-22 Added button released to button class
2024-04-23 Fixed button logic
2024-04-26 Wait for cloud to connect to avoid negative times
    [DateTime_Difference.cpp]
2024-04-26 Vacuum timer works/resets
2024-04-28 Updated Project Plan
    [Coin.stl]
2024-04-29 Servo working in code, added CAD files
    [DispenseTube.stl, DispenseTubeV3.stl, HoleCover.stl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]
2024-04-29 Added KiCad files
    [VacuumATM.fzz, VacuumATM_wCoinDispenser.kicad_pcb, VacuumATM_wCoinDispenser.kicad_sch]
2024-05-03 Shrank hole cover
    [HoleCover.stl]
2024-05-03 Testing alternate print orientation for shaft collar
    [ShaftCollar.stl]
2024-05-03 Made a mount for hall effect sensor.
    [HallMount.stl]
2024-05-03 Removed nonfunctional holes for servo.
    [HoleCover.stl]
2024-05-03 Added alternate tie down for hall effect sesor
    [HallTieDown.stl]
2024-05-03 Added servo mount file
    [Servomount.stl]
2024-05-03 Combining servo and hall sensor
2024-05-05 Hall sensor opens servo after vacuum is returned
2024-05-05 Swapping hall effect sensor for micro switch
    [HallMount.stl, HallTieDown.stl, smSwitchMount.stl]
2024-05-05 Made cam larger, smaller fillets
    [SwitchCam.stl]
2024-05-05 Servo only opens 1x per vacuuming now
2024-05-05 Need more extreme cam profile
    [SwitchCam.stl]
2024-05-06 Added 2nd Photon to just monitor the vacuum charger
2024-05-06 Sending current vac state and time the state changed to adafruit as a string
2024-05-06 Changed LED to breathing
2024-05-06 Turn off other onboard LEDs
2024-05-06 Updated vac button pin
2024-05-07 Switched to sending vac status only
2024-05-07 Start tracking rising, falling edge of vacuum charging
2024-05-08 Made back wall thicker
    [Servomount.stl]
2024-05-08 Added bottom case design for vacstatus electronics
    [VacStatus_CaseBottom.stl]
2024-05-08 Moved charging hole offcenter
    [VacStatus_CaseBottom.stl]
2024-05-08 Added hole to pop out breadboard
    [VacStatus_CaseBottom.stl]
2024-05-10 Tweaked Vacuum Status case
    [CaseBottom.stl, CaseTop.stl]
2024-05-10 Added images of VacStatus case
2024-05-10 First display test
    [Display.stl]
2024-05-10 Adjusted thickness for better light diffusion, changed text
    [Display.stl]
2024-05-10 Reorganizing files
    [CaseBottom.stl, CaseTop.stl, Coin.stl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]
2024-05-10 Getting vacuum chargin status from VacStatus Photon2 instead of from switch
2024-05-10 End of day update
    [VacuumATM.fzz]
2024-05-11 Added DXFs of design panels
    [Back.dxf, FaceSupport.dxf, Faceplate.dxf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]
2024-05-11 Updated Fritzing
    [VacuumATM.fzz]
2024-05-11 Changed units to inches, made vCarve file
    [Back.dxf, FaceSupport.dxf, Faceplate.dxf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]
2024-05-12 Added mount for LED strip.
    [LED_Mount.stl]
2024-05-12 Added laser cut file for acrylic pieces
2024-05-12 Updated faceplate, toolpaths
    [Faceplate.dxf]
2024-05-13 Added LED ring and strip
2024-05-14 Separated LED ring and strip
2024-05-15 Added a mount for the reset button
    [ButtonMount.stl]
2024-05-15 Updated display for better fit and visuals
    [Display.stl]
2024-05-15 Updated LEDmount location
    [LED_Mount.stl]
2024-05-15 Reorganized 3D models
    [Display.stl, LED_Mount.stl]
2024-05-16 Reorganized and updated schematics
    [LED_Mount.stl, VacStatus.fzz, VacuumATM.fzz]
2024-05-17 Updates to KiCAD, images
    [LED_Mount.stl, VacuumATM_wCoinDispenser.kicad_pcb, VacuumATM_wCoinDispenser.kicad_sch]
2024-05-18 Redesigned PCB, made Gerber files
    [VacuumATM_wCoinDispenser-B_Cu.gbr, VacuumATM_wCoinDispenser-B_Mask.gbr, VacuumATM_wCoinDispenser-B_Paste.gbr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]
2024-05-20 Added Gerber files
2024-06-05 Added corrected KiCad footprint and symbol for Photon 2
2024-06-22 Updated KiCAD files
    [VacuumATM_wCoinDispenser.kicad_pcb, VacuumATM_wCoinDispenser.kicad_sch]
2024-06-24 Thickened switch cam, added set screw option.
    [SwitchCam.stl, SwitchCam_wSetScrew.stl]
2024-06-24 Improved LED colors and feel.
2024-10-06 Fixed breathing LED jitter.
    [Vacuum_Status.cpp]
2025-01-10 Added watchdog timer
